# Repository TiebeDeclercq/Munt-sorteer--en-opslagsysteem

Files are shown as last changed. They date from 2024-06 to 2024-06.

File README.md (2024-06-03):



<!-- PROJECT LOGO -->
<br />
<div align="center">
  <a href="https://github.com/othneildrew/Best-README-Template">
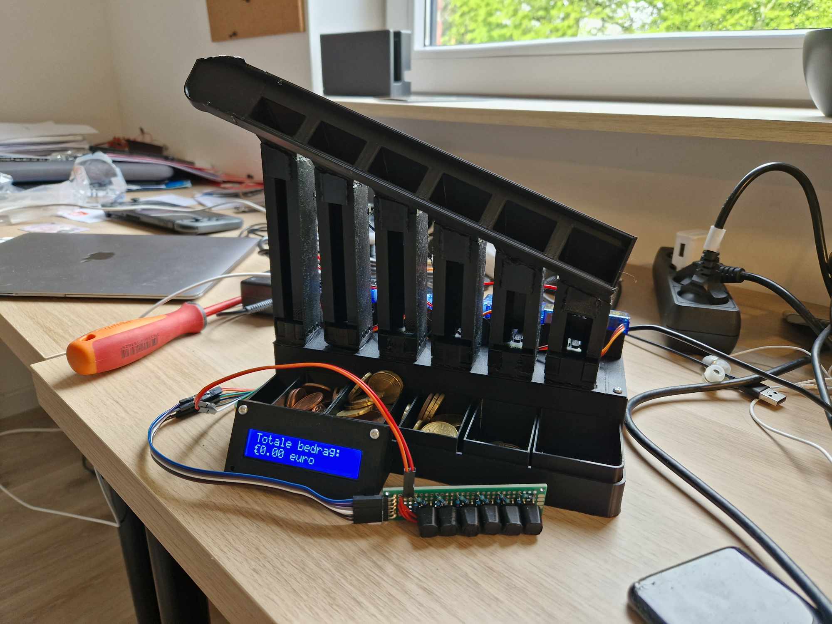
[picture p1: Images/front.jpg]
front sorter
    
  </a>

  <h3 align="center">Coin sorting and storage system</h3>

  <p align="center">
    A coin-counting, storing, and dispensing system.
    <br />
    <a href="https://giptiebedeclercq.wordpress.com/"><strong>View the blog »</strong></a>
    <br />
    <br />
  </p>
</div>

<!-- ABOUT THE PROJECT -->
## About The Project

My design is a coin sorting and storage system aimed at effectively addressing the issue of loose change in the household. By storing all your coins in one central location, all the inconveniences of scattered small change are eliminated, and you have an accurate overview of your available loose change at all times. In this document, I will meticulously walk through the various phases of the project, detailing the development and implementation of the coin sorting and storage system step by step. All necessary information, including components and diagrams, is included in my document, accompanied by comprehensive explanations for a clear overview of the entire process.

## Download the software
This is the general software to control the coinsorting system for simply storing you're coins
<p float="left">
  
  
  
</p>

This is sofware/game to play flappy bird but you can play with multiple people and compete against eatchother 



<p align="right">(<a href="#readme-top">back to top</a>)</p>

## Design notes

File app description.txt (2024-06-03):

Deze app is een toevoeging op het muntsorteer- en opslagsysteem gemaakt door Ti3b3:

Krijg een overzicht van al je kleingeld
Kies hoeveel kleingeld je wilt uitwerpen
Personaliseer je muntsorteerder tot je behoefte!

MAXIMAAL AANTAL KLEINGELD INSTELLEN
Wil je maar een maximaal aantal geld toelaten in het systeem? Geen probleem dit kan je allemaal instellen via deze app

EEN EXACTE HOEVEELHEID KLEINGELD UITWERPEN
Via deze app kan je een hoeveelheid ingeven en er zal berekent worden of dit mogelijk is en zal dan uitgeworpen worden!

ZIT ER EEN PROBLEEM IN JE OPSTELLING?
Je kan de waarden van je geldsysteem aanpassen als ze verkeerd gedecteerd zijn en ook je maximale waarden aanpassen!

EEN ANDERE WERKINGSMODUS INSTELLEN?
Je kan je werkingsmodus instellen via de app als je bevoorbeeld wilt dat hij enkel sorteert en niet opslaat of geluid maakt bij het uitwerpen.

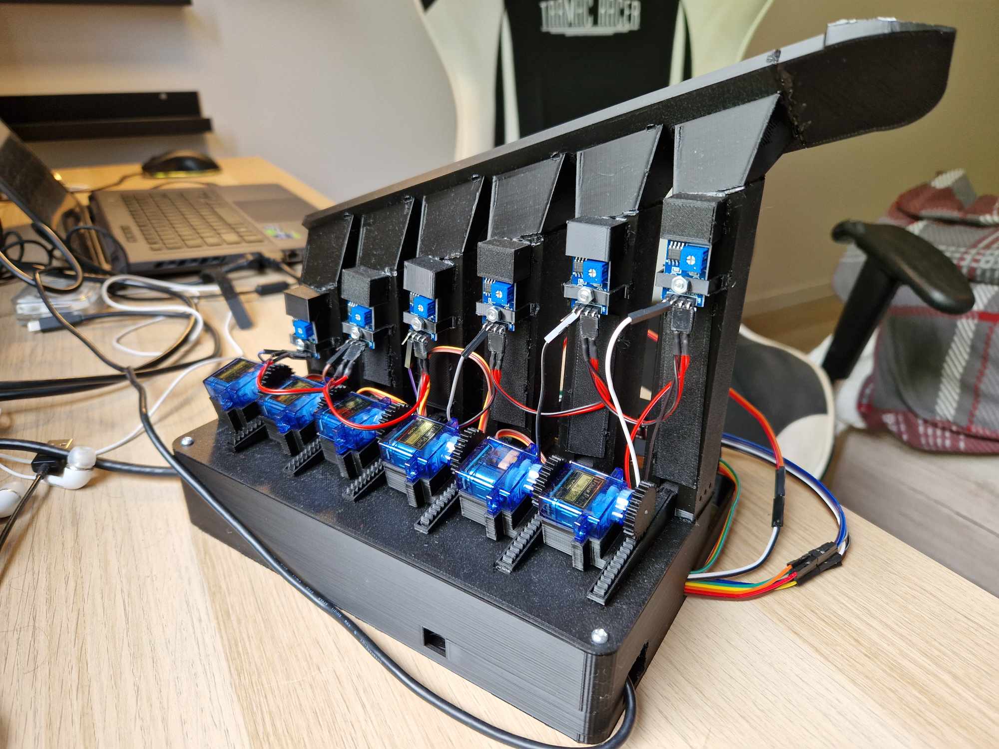
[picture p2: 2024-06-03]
Images/back.jpg

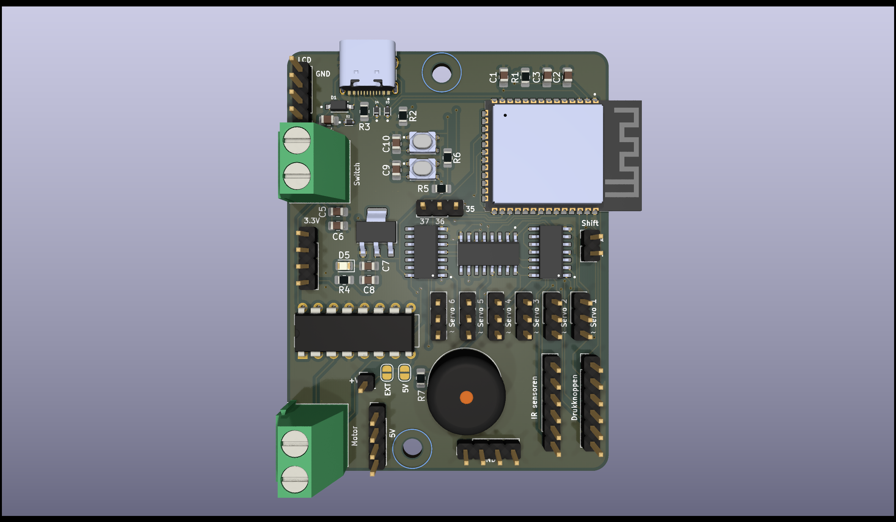
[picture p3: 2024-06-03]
Images/MuntsorteerderESPbord.png

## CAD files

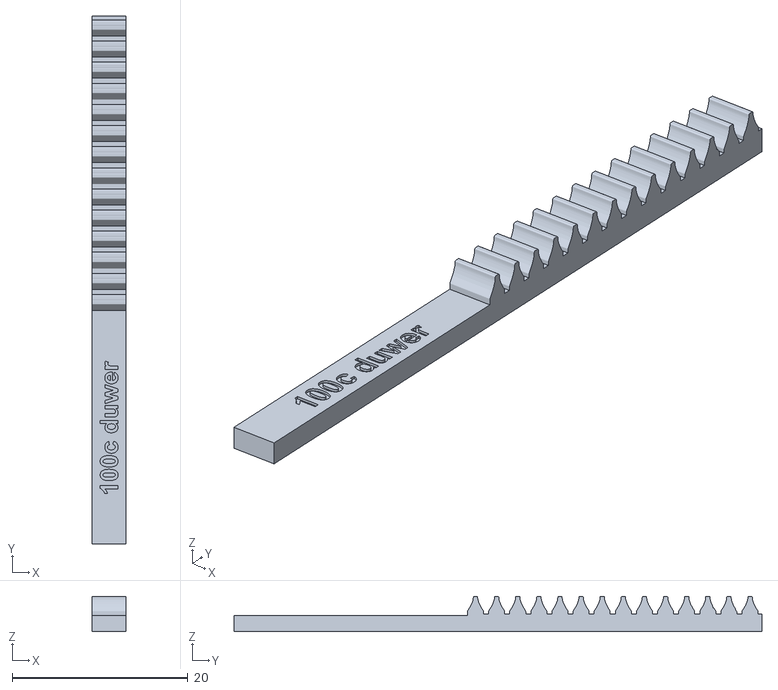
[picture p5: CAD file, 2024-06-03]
Printables/1eurSlider.stl
3.85 x 60.0 x 4.02

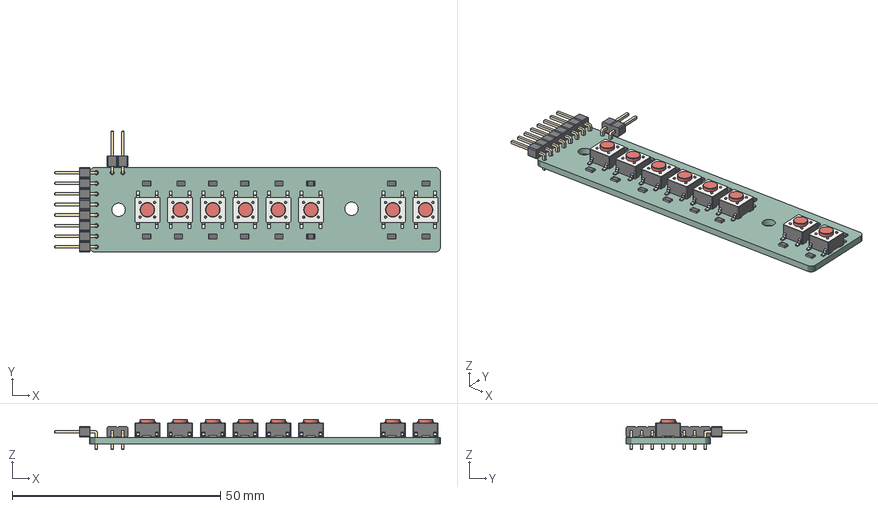
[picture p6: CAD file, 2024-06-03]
SeperatePCB's/ButtonsPCB/ButtonsPCB.step
92.6 x 29.1 x 7.30 mm
_autosave-ButtonsPCB PCB

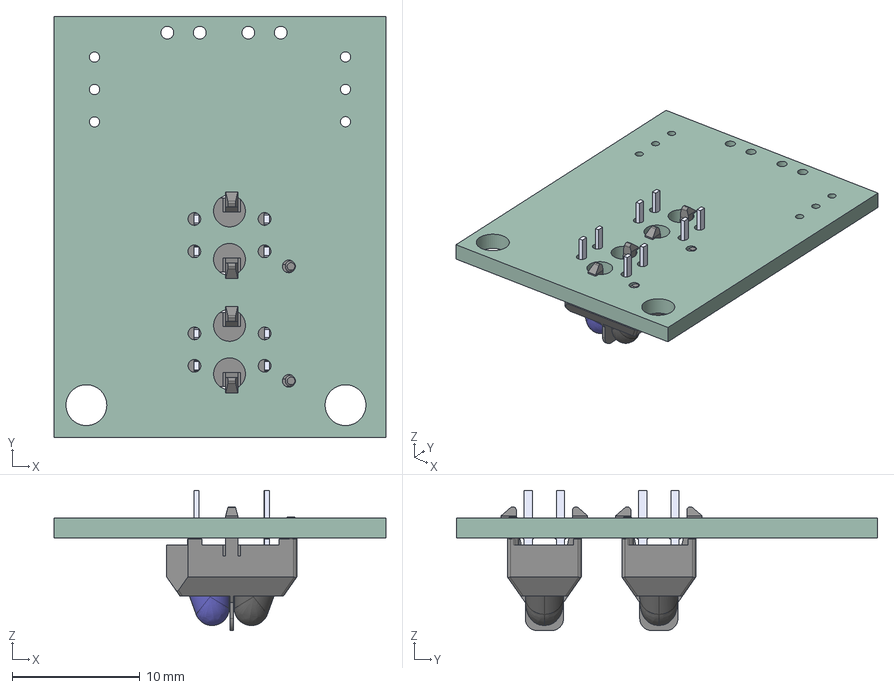
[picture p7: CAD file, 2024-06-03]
SeperatePCB's/IrBoards/IrBoards.step
26.0 x 33.0 x 11.0 mm
_autosave-IrBoards PCB

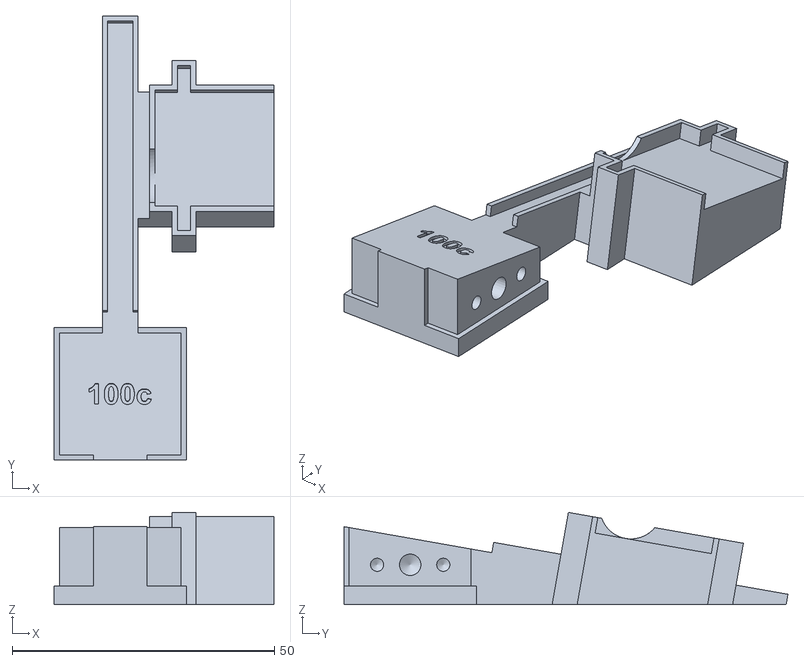
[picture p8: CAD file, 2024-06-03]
Printables/1eurPushout.stl
41.9 x 84.7 x 17.6

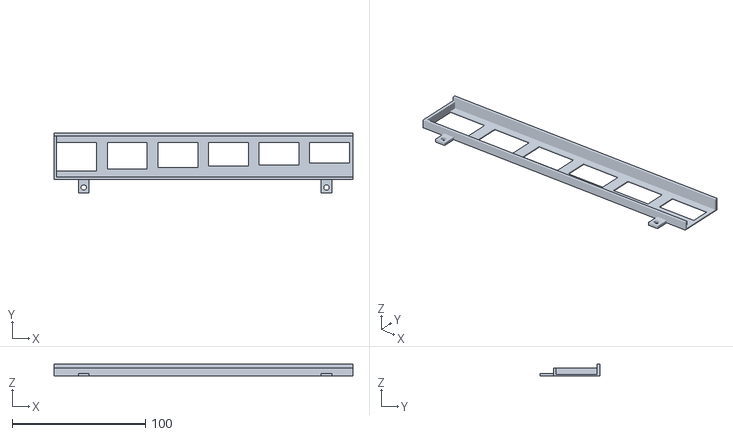
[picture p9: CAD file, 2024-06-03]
Printables/Sorter.stl
224.5 x 44.8 x 9.00

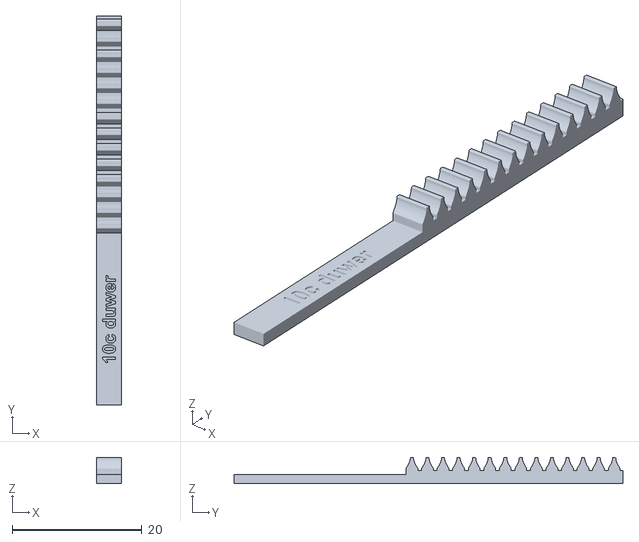
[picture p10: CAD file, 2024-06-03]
Printables/10centSlider.stl
3.85 x 60.0 x 4.02

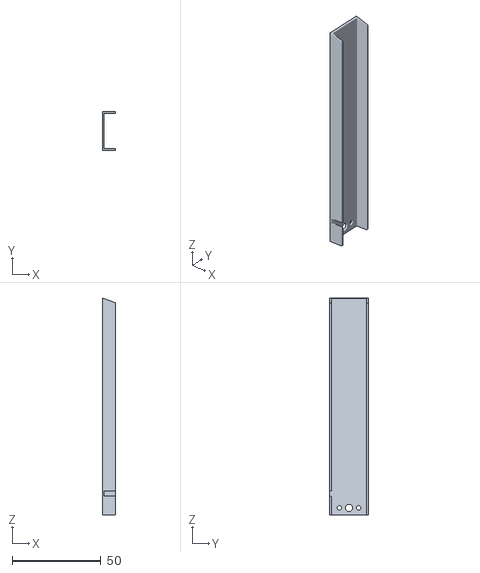
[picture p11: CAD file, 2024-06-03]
Printables/10centRightWall.stl
7.50 x 21.8 x 122.2

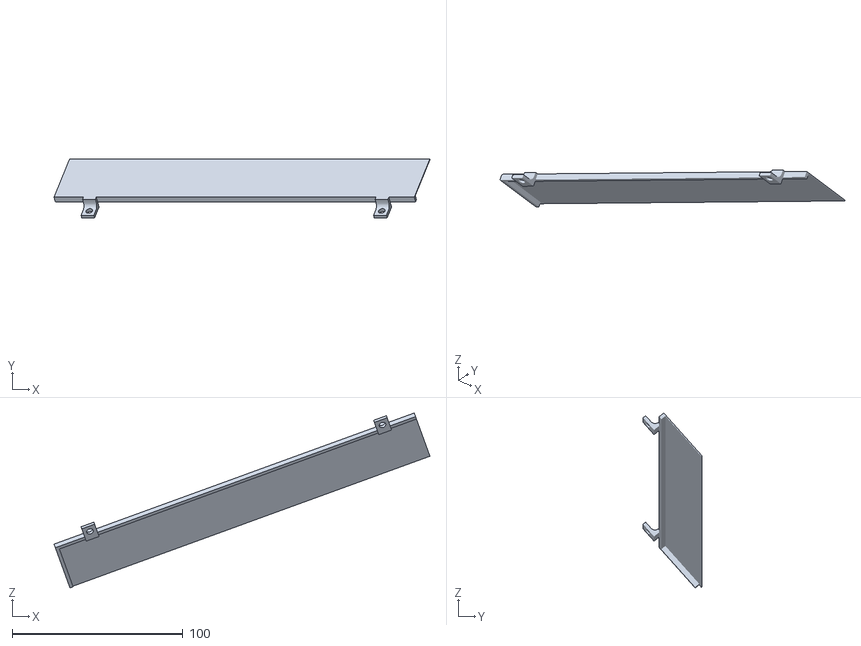
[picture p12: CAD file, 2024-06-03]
Printables/SorterCover.stl
220.2 x 34.5 x 102.5

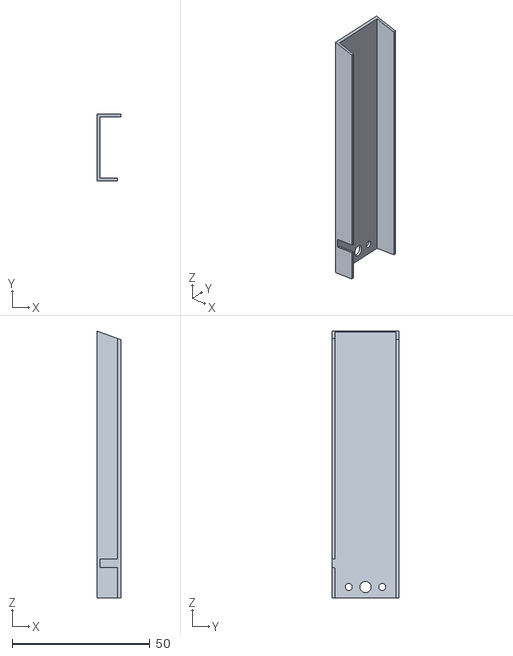
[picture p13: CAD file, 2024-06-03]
Printables/20centRightWall.stl
8.70 x 24.2 x 96.7

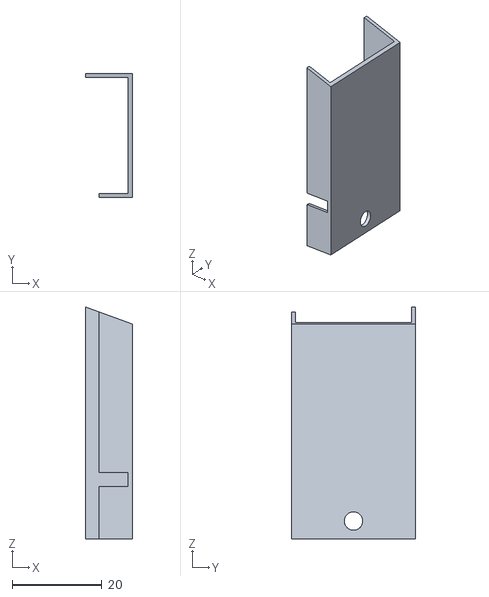
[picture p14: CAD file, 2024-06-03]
Printables/2eurLeftWall.stl
10.4 x 27.8 x 51.7

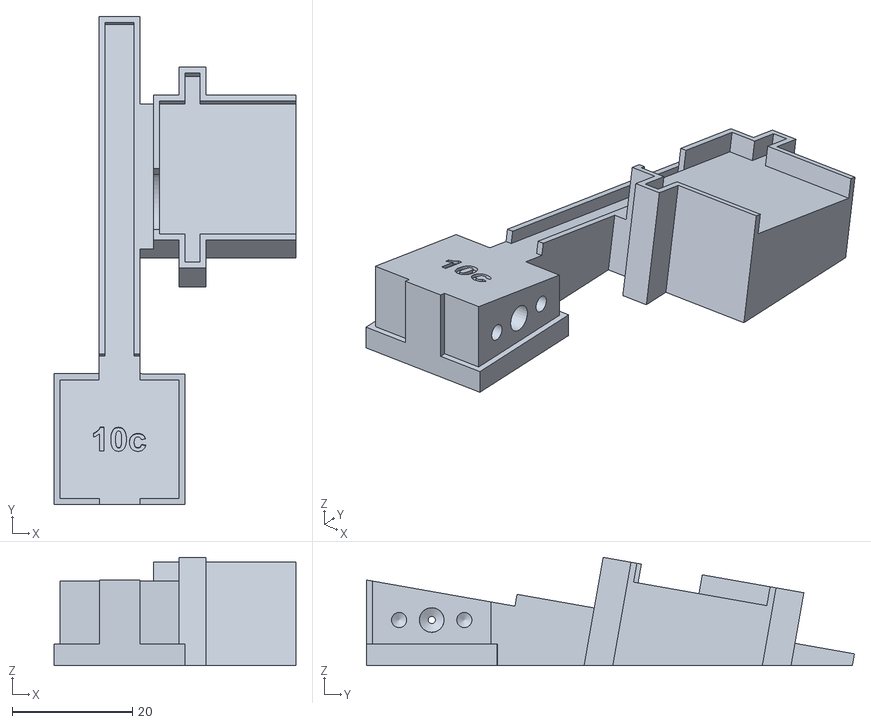
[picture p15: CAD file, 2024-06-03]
Printables/10cPushout.stl
40.2 x 81.2 x 18.0

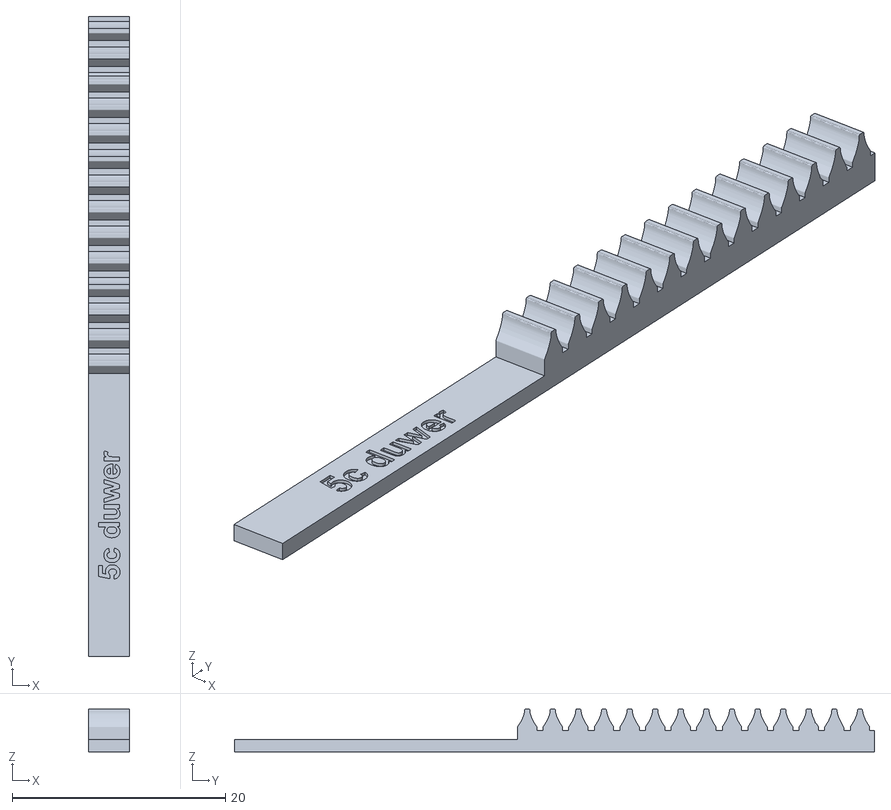
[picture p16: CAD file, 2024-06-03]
Printables/5centSlider.stl
3.85 x 60.0 x 4.02

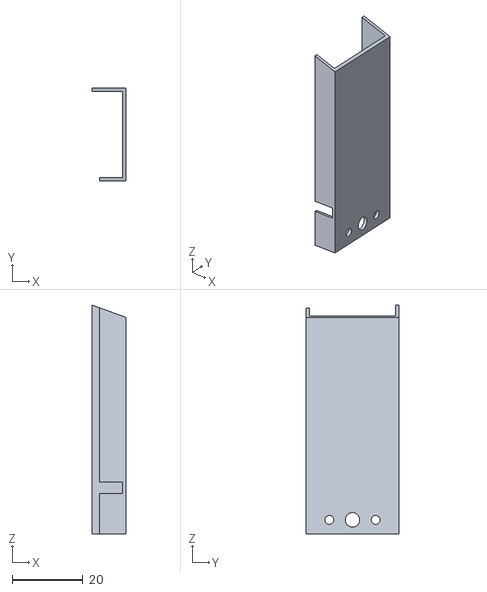
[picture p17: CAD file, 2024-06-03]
Printables/50centLeftWall.stl
9.70 x 26.2 x 64.9

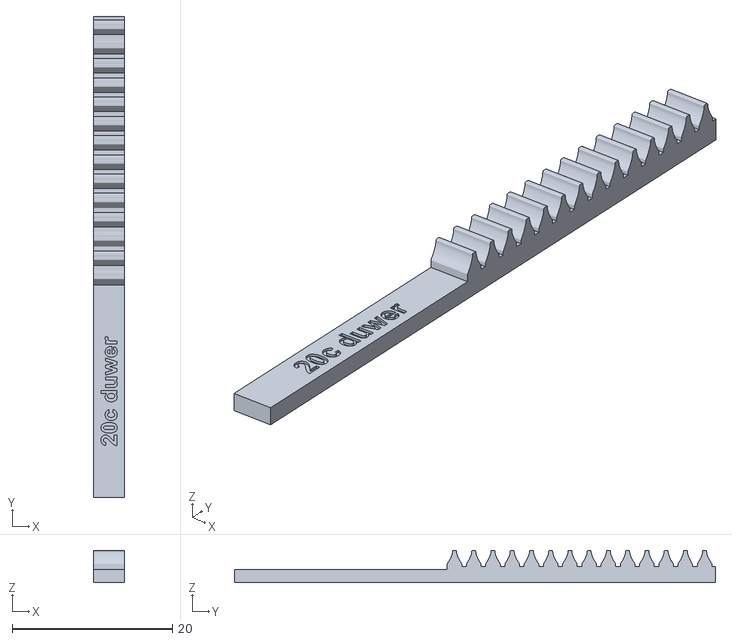
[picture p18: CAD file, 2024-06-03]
Printables/20centSlider.stl
3.85 x 60.0 x 4.02

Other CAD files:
Printables/50centRightWall.stl
Printables/2eurSlider.stl
Printables/5centRightWall.stl
Printables/2eurPushout.stl
Printables/10centLeftWall.stl
Printables/10centTunnel.stl
Printables/1eurLeftWall.stl
Printables/1eurRightWall.stl
Printables/1eurTunnel.stl
Printables/20centLeftWall.stl
Printables/20centPushout.stl
Printables/20centTunnel.stl
Printables/2eurRightWall.stl
Printables/2eurTunnel.stl
Printables/50centPushout.stl
Printables/50centSlider.stl
Printables/50centTunnel.stl
Printables/5centLeftWall.stl
Printables/5centPushout.stl
Printables/5centTunnel.stl
Printables/BoxWithButtons.stl
Printables/Cover.stl
Printables/IrHead.stl
Printables/IrHolder.stl
Printables/LCDcover.stl
Printables/Lid.stl
Printables/ServoGear.stl

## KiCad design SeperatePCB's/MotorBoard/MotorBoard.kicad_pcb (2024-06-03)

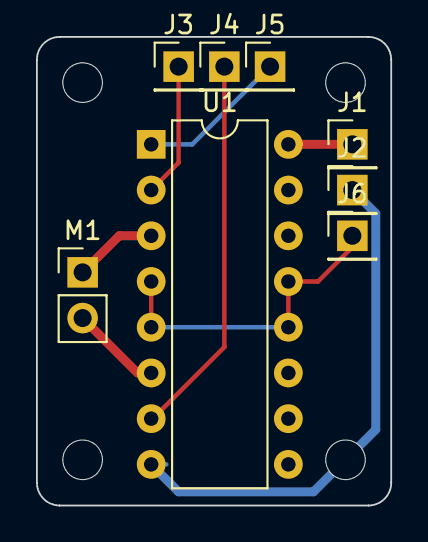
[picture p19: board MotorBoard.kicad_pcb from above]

Board: 2 copper layers, 19.7 x 26.0 mm, 12 parts (0 on the bottom side), 8 nets.

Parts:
H1, H2, H3, H4: MountingHole; MountingHole_2.2mm_M2
J1, J2, J3, J4, J5, J6: Conn_01x01_Pin; PinHeader_1x01_P2.54mm_Vertical
M1: Motor_DC; PinHeader_1x02_P2.54mm_Vertical
U1: L293D; DIP-16_W7.62mm

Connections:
unnamed: J1.1, U1.16 (VCC1)
unnamed: J2.1, U1.8 (VCC2)
unnamed: J3.1, U1.2 (1A)
unnamed: J4.1, U1.7 (2A)
unnamed: J5.1, U1.1 (EN1,2)
unnamed: J6.1, U1.4 (GND), U1.5 (GND), U1.12 (GND), U1.13 (GND)
unnamed: M1.1 (+), U1.3 (1Y)
unnamed: M1.2 (-), U1.6 (2Y)

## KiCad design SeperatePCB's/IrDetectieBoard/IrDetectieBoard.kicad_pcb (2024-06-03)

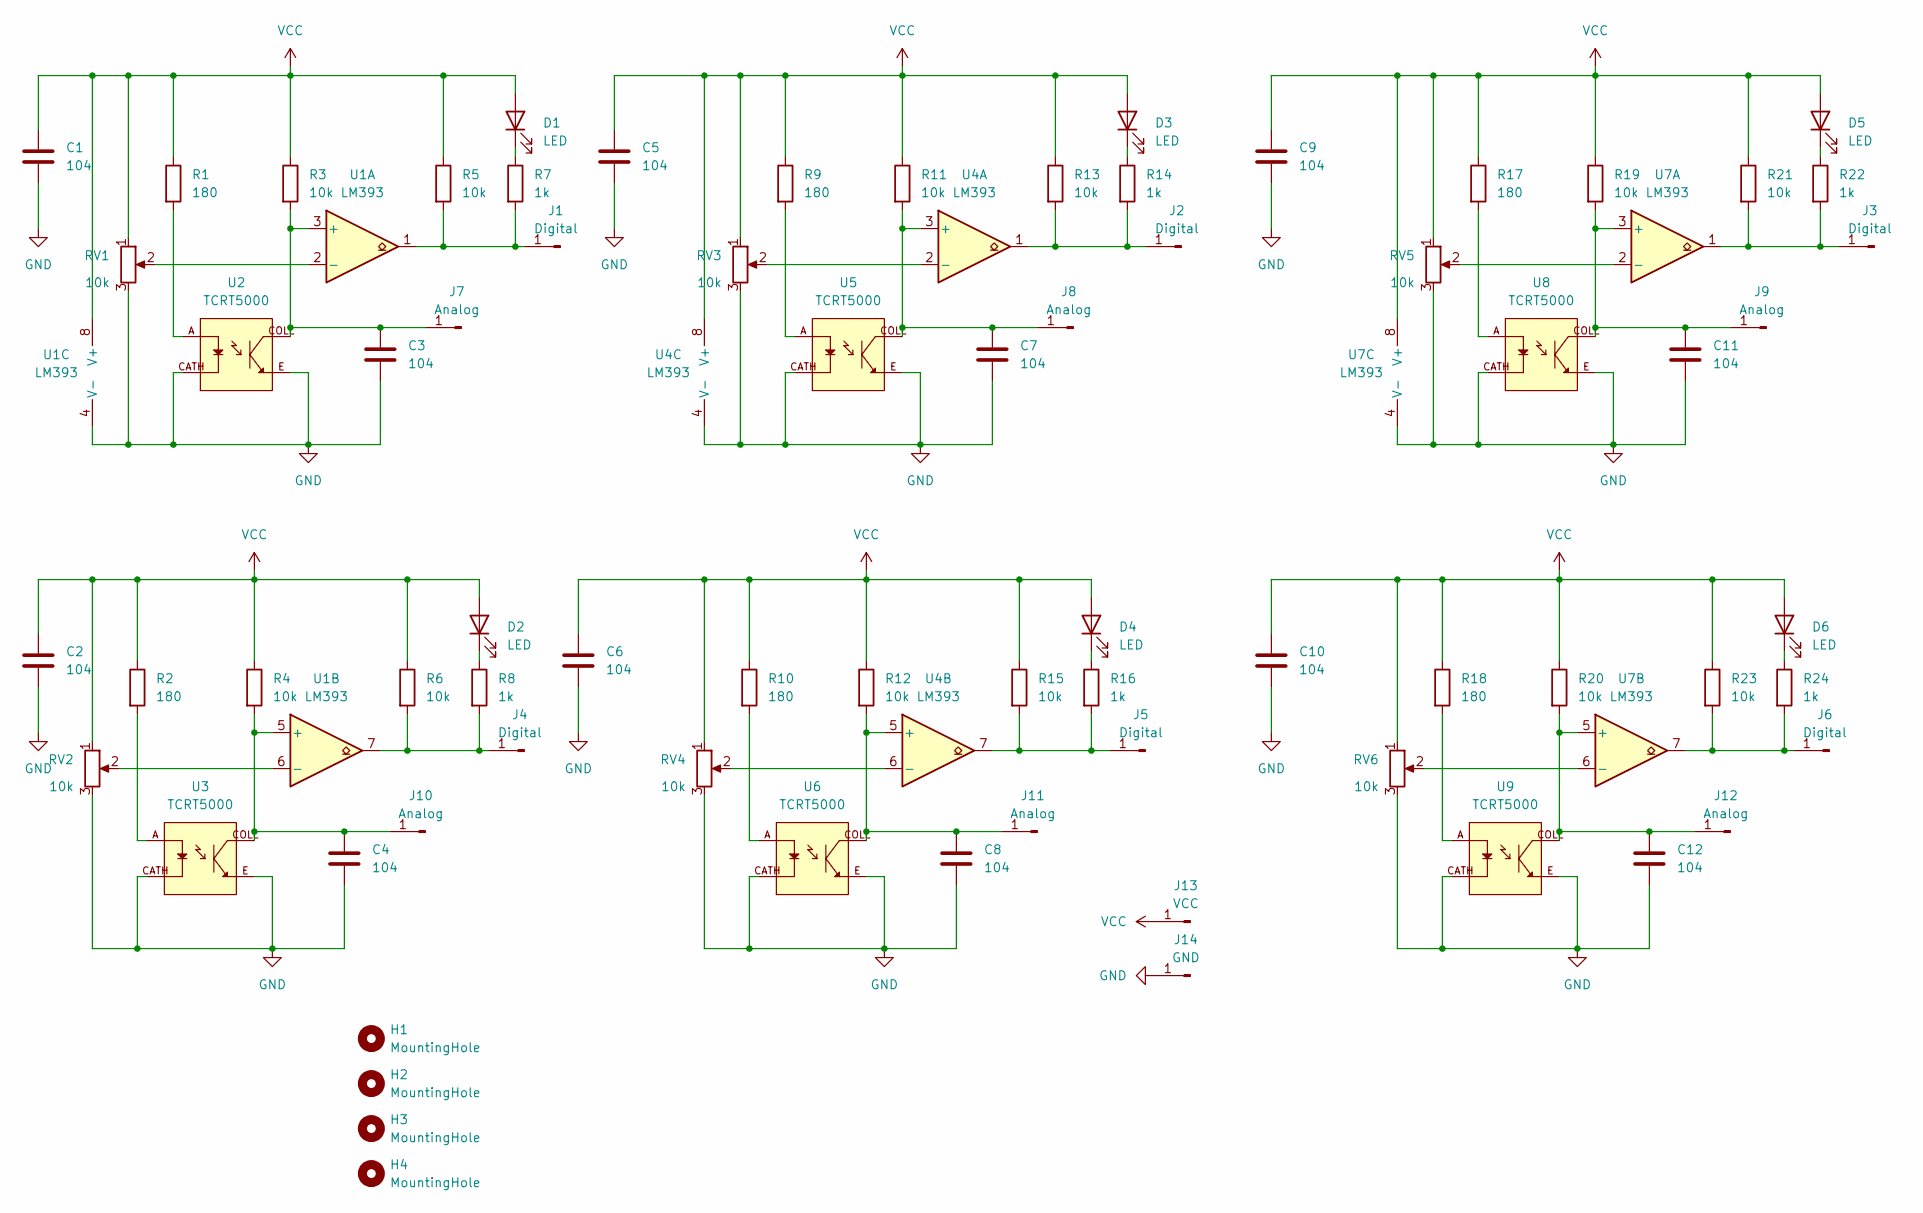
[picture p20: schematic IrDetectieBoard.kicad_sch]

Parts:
C1, C2, C3, C4, C5, C6, C7, C8, C9, C10, C11, C12: 104; C_0805_2012Metric_Pad1.18x1.45mm_HandSolder
D1, D2, D3, D4, D5, D6: LED; LED_0805_2012Metric_Pad1.15x1.40mm_HandSolder
H1, H2, H3, H4: MountingHole; MountingHole_2.2mm_M2
J1, J2, J3, J4, J5, J6: Digital; PinHeader_1x01_P2.54mm_Vertical
J7, J8, J9, J10, J11, J12: Analog; PinHeader_1x01_P2.54mm_Vertical
J13: VCC; PinHeader_1x01_P2.54mm_Vertical
J14: GND; PinHeader_1x01_P2.54mm_Vertical
R1, R2, R9, R10, R17, R18: 180; R_0805_2012Metric_Pad1.20x1.40mm_HandSolder
R3, R4, R5, R6, R11, R12, R13, R15, R19, R20, R21, R23: 10k; R_0805_2012Metric_Pad1.20x1.40mm_HandSolder
R7, R8, R14, R16, R22, R24: 1k; R_0805_2012Metric_Pad1.20x1.40mm_HandSolder
RV1, RV2, RV3, RV4, RV5, RV6: 10k; Potentiometer_Bourns_3296W_Vertical
U1, U4, U7: LM393; SO-8_3.9x4.9mm_P1.27mm
U2, U3, U5, U6, U8, U9: TCRT5000; PARTREV 1.7

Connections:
GND: C1.2, C2.2, C3.2, C4.2, C5.2, C6.2, C7.2, C8.2, C9.2, C10.2, C11.2, C12.2, J14.1, RV1.3, RV2.3, RV3.3, RV4.3, RV5.3, RV6.3, U1.4 (V-), U2.CATH, U2.E, U3.CATH, U3.E, U4.4 (V-), U5.CATH, U5.E, U6.CATH, U6.E, U7.4 (V-), U8.CATH, U8.E, U9.CATH, U9.E
unnamed: D1.1 (K), R7.1
unnamed: D2.1 (K), R8.1
unnamed: D3.1 (K), R14.1
unnamed: D4.1 (K), R16.1
unnamed: D5.1 (K), R22.1
unnamed: D6.1 (K), R24.1
unnamed: J1.1, R5.2, R7.2, U1.1
unnamed: J2.1, R13.2, R14.2, U4.1
unnamed: J3.1, R21.2, R22.2, U7.1
unnamed: J4.1, R6.2, R8.2, U1.7
unnamed: J5.1, R15.2, R16.2, U4.7
unnamed: J6.1, R23.2, R24.2, U7.7
unnamed: C3.1, J7.1, R3.2, U1.3 (+), U2.COLL
unnamed: C7.1, J8.1, R11.2, U4.3 (+), U5.COLL
unnamed: C11.1, J9.1, R19.2, U7.3 (+), U8.COLL
unnamed: C4.1, J10.1, R4.2, U1.5 (+), U3.COLL
unnamed: C8.1, J11.1, R12.2, U4.5 (+), U6.COLL
unnamed: C12.1, J12.1, R20.2, U7.5 (+), U9.COLL
unnamed: R1.2, U2.A
unnamed: R2.2, U3.A
unnamed: R9.2, U5.A
unnamed: R10.2, U6.A
unnamed: R17.2, U8.A
unnamed: R18.2, U9.A
unnamed: RV1.2, U1.2 (-)
unnamed: RV2.2, U1.6 (-)
unnamed: RV3.2, U4.2 (-)
unnamed: RV4.2, U4.6 (-)
unnamed: RV5.2, U7.2 (-)
unnamed: RV6.2, U7.6 (-)
VCC: C1.1, C2.1, C5.1, C6.1, C9.1, C10.1, D1.2 (A), D2.2 (A), D3.2 (A), D4.2 (A), D5.2 (A), D6.2 (A), J13.1, R1.1, R2.1, R3.1, R4.1, R5.1, R6.1, R9.1, R10.1, R11.1, R12.1, R13.1, R15.1, R17.1, R18.1, R19.1, R20.1, R21.1, R23.1, RV1.1, RV2.1, RV3.1, RV4.1, RV5.1, RV6.1, U1.8 (V+), U4.8 (V+), U7.8 (V+)

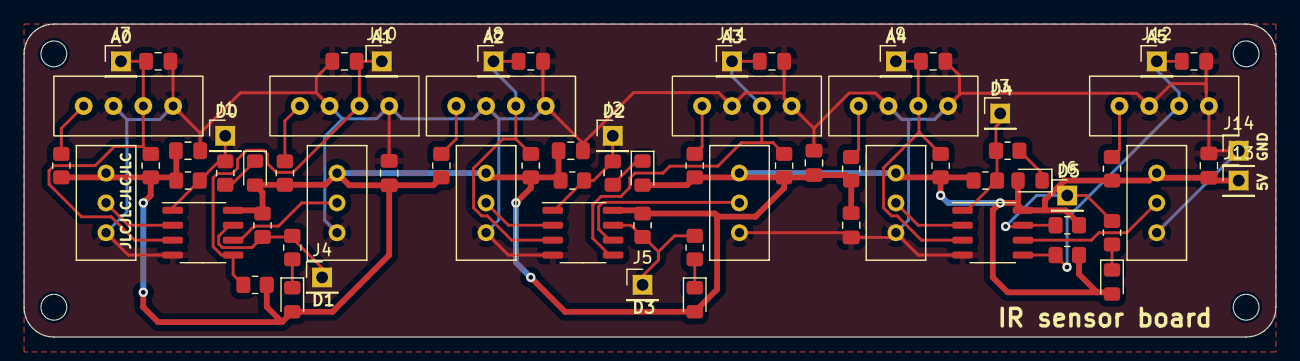
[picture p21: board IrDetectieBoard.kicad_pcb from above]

Board: 2 copper layers, 106.7 x 26.7 mm, 75 parts (0 on the bottom side), 32 nets.

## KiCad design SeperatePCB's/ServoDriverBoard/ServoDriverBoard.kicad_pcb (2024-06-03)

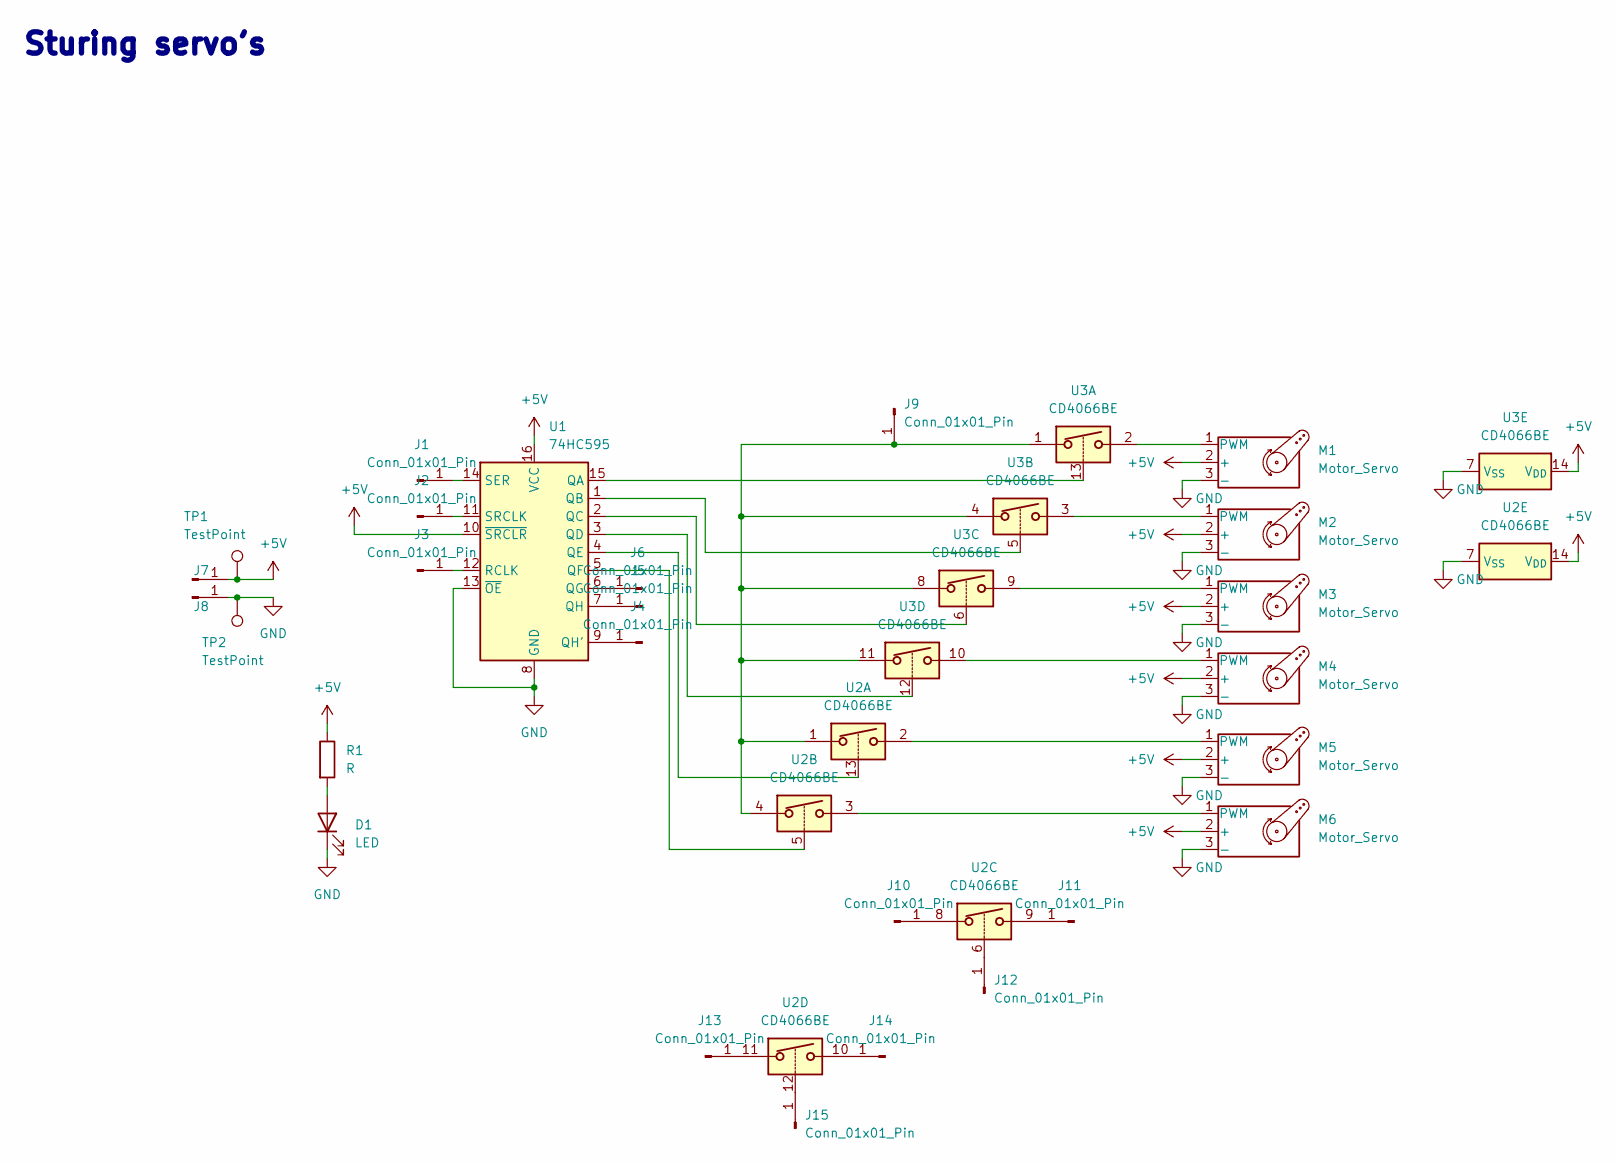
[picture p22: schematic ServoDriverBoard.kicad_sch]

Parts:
D1: LED; LED_0805_2012Metric_Pad1.15x1.40mm_HandSolder
J1, J2, J3, J4, J5, J6, J7, J8, J9, J10, J11, J12, J13, J14, J15: Conn_01x01_Pin; PinHeader_1x01_P2.54mm_Vertical
M1, M2, M3, M4, M5, M6: Motor_Servo; PinHeader_1x03_P2.54mm_Vertical
R1: R; R_0805_2012Metric_Pad1.20x1.40mm_HandSolder
TP1, TP2: TestPoint; TestPoint_Pad_D1.5mm
U1: 74HC595; DIP-16_W7.62mm_Socket
U2, U3: CD4066BE; DIP-14_W7.62mm_Socket

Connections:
+5V: J7.1, M1.2 (+), M2.2 (+), M3.2 (+), M4.2 (+), M5.2 (+), M6.2 (+), R1.1, TP1.1, U1.10 (~SRCLR), U1.16 (VCC), U2.14 (V_{DD}), U3.14 (V_{DD})
GND: D1.1 (K), J8.1, M1.3 (-), M2.3 (-), M3.3 (-), M4.3 (-), M5.3 (-), M6.3 (-), TP2.1, U1.8 (GND), U1.13 (~OE), U2.7 (V_{SS}), U3.7 (V_{SS})
unnamed: D1.2 (A), R1.2
unnamed: J1.1, U1.14 (SER)
unnamed: J2.1, U1.11 (SRCLK)
unnamed: J3.1, U1.12 (RCLK)
unnamed: J4.1, U1.9 (QH')
unnamed: J5.1, U1.7 (QH)
unnamed: J6.1, U1.6 (QG)
unnamed: J9.1, U2.1, U2.4, U3.1, U3.4, U3.8, U3.11
unnamed: J10.1, U2.8
unnamed: J11.1, U2.9
unnamed: J12.1, U2.6
unnamed: J13.1, U2.11
unnamed: J14.1, U2.10
unnamed: J15.1, U2.12
unnamed: M1.1 (PWM), U3.2
unnamed: M2.1 (PWM), U3.3
unnamed: M3.1 (PWM), U3.9
unnamed: M4.1 (PWM), U3.10
unnamed: M5.1 (PWM), U2.2
unnamed: M6.1 (PWM), U2.3
unnamed: U1.15 (QA), U3.13
unnamed: U1.1 (QB), U3.5
unnamed: U1.2 (QC), U3.6
unnamed: U1.3 (QD), U3.12
unnamed: U1.4 (QE), U2.13
unnamed: U1.5 (QF), U2.5

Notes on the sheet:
Sturing servo's

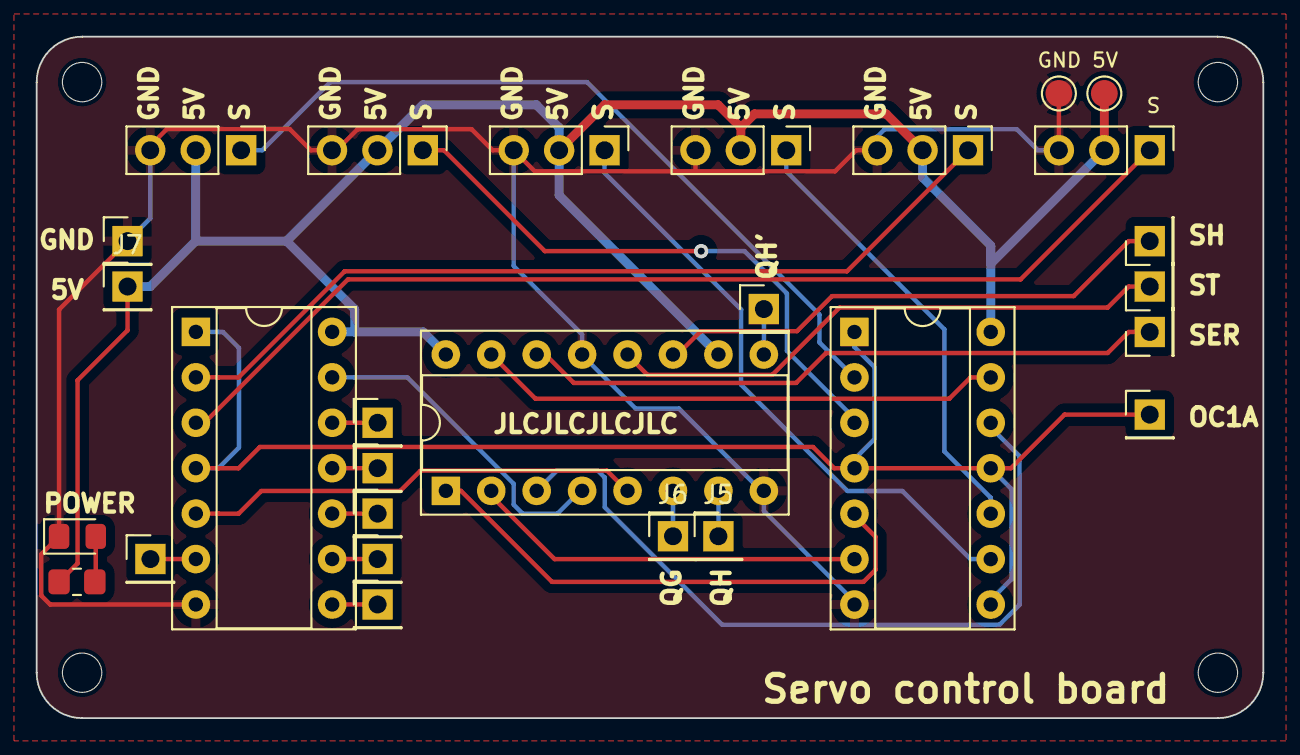
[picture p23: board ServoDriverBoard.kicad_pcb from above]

Board: 2 copper layers, 68.6 x 38.1 mm, 32 parts (0 on the bottom side), 28 nets.

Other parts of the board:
H1, H2, H3, H4: MountingHole; MountingHole_2.2mm_M2

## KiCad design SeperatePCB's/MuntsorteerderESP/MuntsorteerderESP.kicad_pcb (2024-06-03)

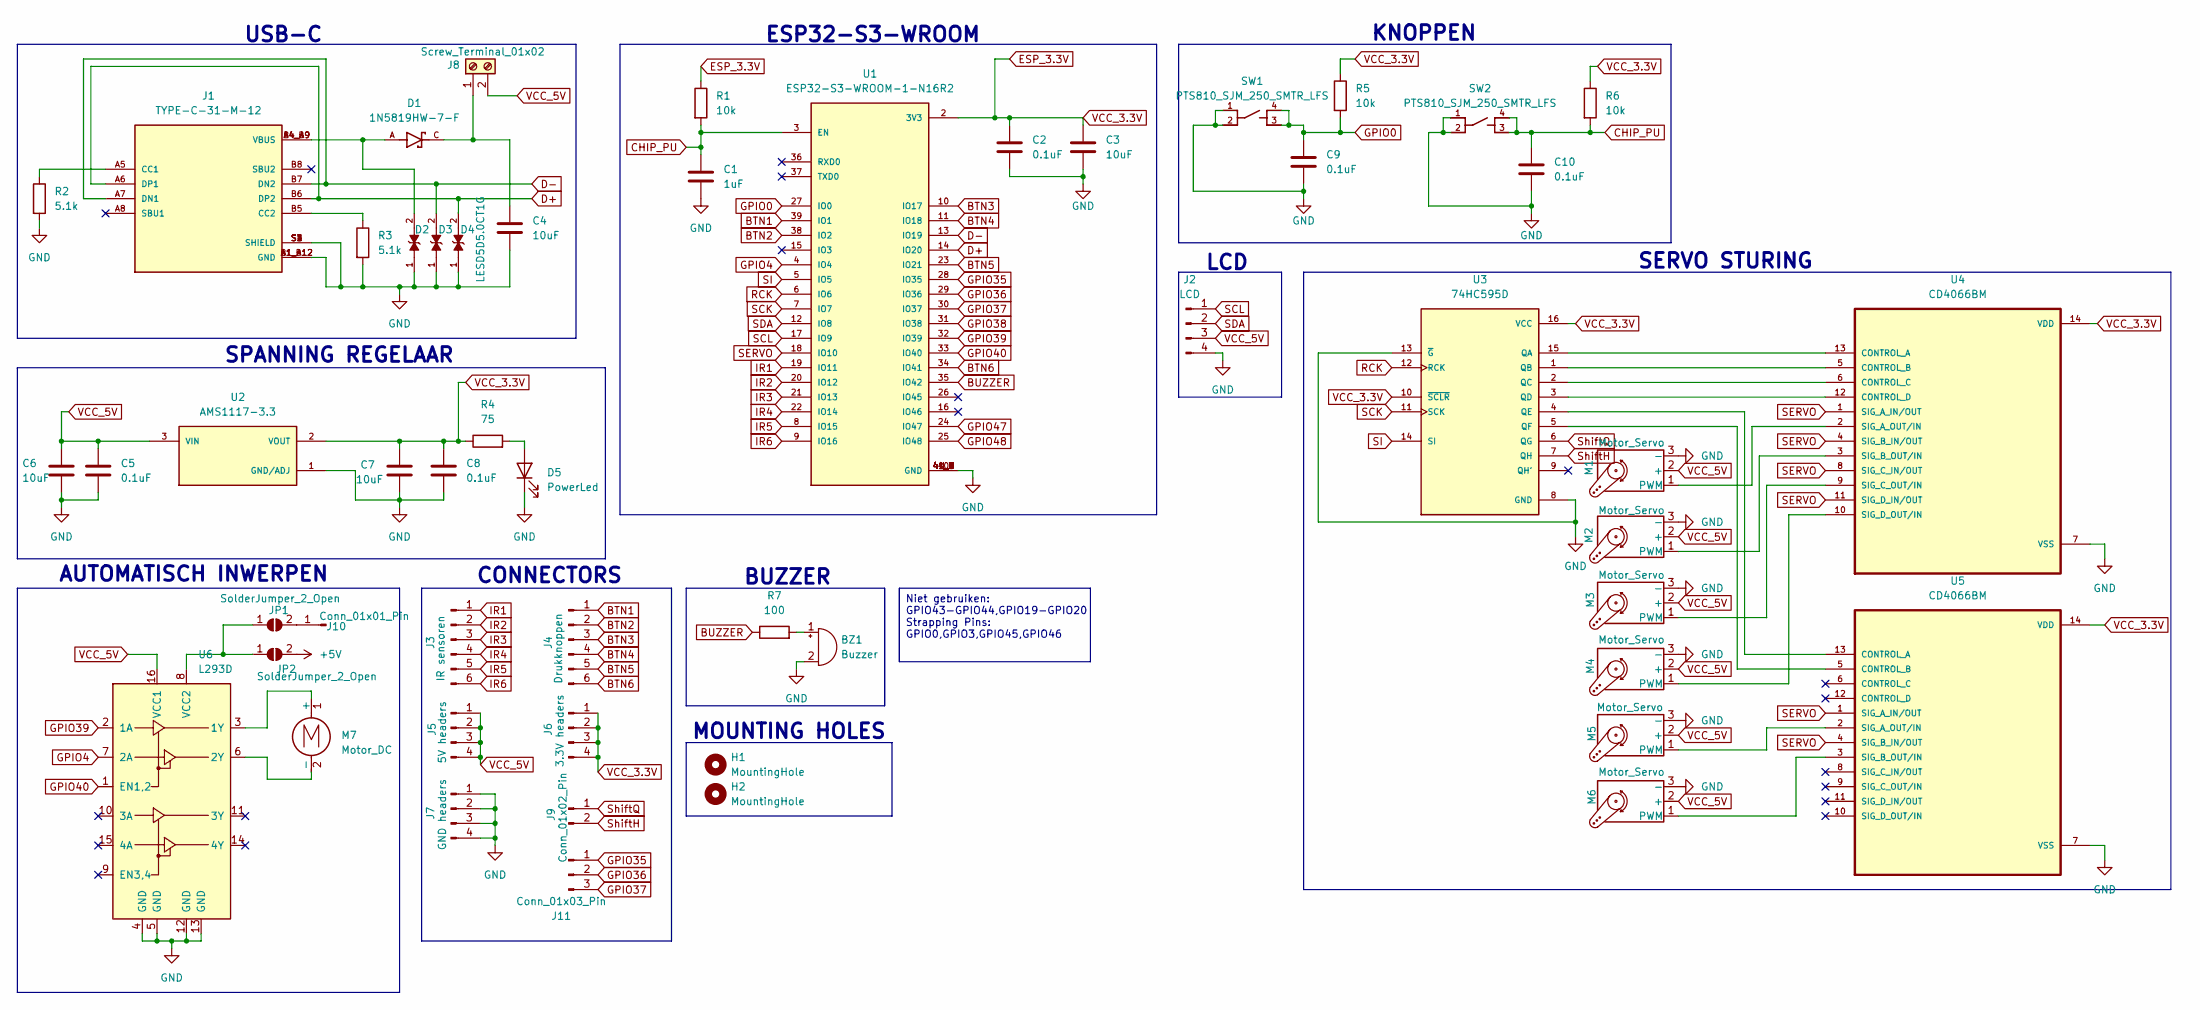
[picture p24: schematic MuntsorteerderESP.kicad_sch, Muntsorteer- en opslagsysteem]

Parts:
BZ1: Buzzer; Buzzer_12x9.5RM7.6
C1: 1uF; C_0805_2012Metric_Pad1.18x1.45mm_HandSolder
C2, C5, C8, C9, C10: 0.1uF; C_0805_2012Metric_Pad1.18x1.45mm_HandSolder
C3, C4, C6, C7: 10uF; C_0805_2012Metric_Pad1.18x1.45mm_HandSolder
D1: 1N5819HW-7-F; SOD3715X145N; PARTREV 18-2
D2, D3, D4: LESD5D5.0CT1G; TVS_LESD5D5.0CT1G; PARTREV O
D5: PowerLed; LED_0805_2012Metric
H1, H2: MountingHole; MountingHole_3.2mm_M3
J1: TYPE-C-31-M-12; HRO_TYPE-C-31-M-12; PARTREV 2020.12.08
J2: LCD; PinHeader_1x04_P2.54mm_Vertical
J3: IR sensoren; PinHeader_1x06_P2.54mm_Vertical
J4: Drukknoppen; PinHeader_1x06_P2.54mm_Vertical
J5: 5V headers; PinHeader_1x04_P2.54mm_Vertical
J6: 3.3V headers; PinHeader_1x04_P2.54mm_Vertical
J7: GND headers; PinHeader_1x04_P2.54mm_Vertical
J8: Screw_Terminal_01x02; TerminalBlock_Phoenix_MKDS-1,5-2-5.08_1x02_P5.08mm_Horizont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
J9: Conn_01x02_Pin; PinHeader_1x02_P2.54mm_Vertical
J10: Conn_01x01_Pin; PinHeader_1x01_P2.54mm_Vertical
J11: Conn_01x03_Pin; PinHeader_1x03_P2.54mm_Vertical
JP1, JP2: SolderJumper_2_Open; SolderJumper-2_P1.3mm_Open_RoundedPad1.0x1.5mm
M1, M2, M3, M4, M5, M6: Motor_Servo; PinHeader_1x03_P2.54mm_Vertical
M7: Motor_DC; TerminalBlock_Phoenix_MKDS-1,5-2-5.08_1x02_P5.08mm_Horizont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
R1, R5, R6: 10k; R_0805_2012Metric_Pad1.20x1.40mm_HandSolder
R2, R3: 5.1k; R_0805_2012Metric_Pad1.20x1.40mm_HandSolder
R4: 75; R_0805_2012Metric_Pad1.20x1.40mm_HandSolder
R7: 100; R_0805_2012Metric_Pad1.20x1.40mm_HandSolder
SW1, SW2: PTS810_SJM_250_SMTR_LFS; SW_PTS810_SJM_250_SMTR_LFS
U1: ESP32-S3-WROOM-1-N16R2; XCVR_ESP32-S3-WROOM-1-N16R2; PARTREV v1.0
U2: AMS1117-3.3; SOT229P700X180-4N; PARTREV N/A
U3: 74HC595D; SOP127P600X175-16N; PARTREV 4.0
U4, U5: CD4066BM; SOIC127P600X175-14N
U6: L293D; DIP-16_W7.62mm

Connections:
+5V: JP2.2 (B)
BTN1: J4.1, U1.39 (IO1)
BTN2: J4.2, U1.38 (IO2)
BTN3: J4.3, U1.10 (IO17)
BTN4: J4.4, U1.11 (IO18)
BTN5: J4.5, U1.23 (IO21)
BTN6: J4.6, U1.34 (IO41)
BUZZER: R7.1, U1.35 (IO42)
CHIP_PU: C1.1, C10.1, R1.2, R6.2, SW2.3, SW2.4, U1.3 (EN)
D+: D4.2, J1.A6 (DP1), J1.B6 (DP2), U1.14 (IO20)
D-: D3.2, J1.A7 (DN1), J1.B7 (DN2), U1.13 (IO19)
ESP_3.3V: C2.1, C3.1, C7.1, C8.1, J6.1, J6.2, J6.3, J6.4, R1.1, R4.1, R5.1, R6.1, U1.2 (3V3), U2.2 (VOUT), U3.10 (~SCLR), U3.16 (VCC), U4.14 (VDD), U5.14 (VDD)
GND: BZ1.2 (+), C1.2, C2.2, C3.2, C4.2, C5.2, C6.2, C7.2, C8.2, C9.2, C10.2, D2.1, D3.1, D4.1, D5.1 (K), J1.A1_B12 (GND), J1.B1_A12 (GND), J1.S1 (SHIELD), J1.S2 (SHIELD), J1.S3 (SHIELD), J1.S4 (SHIELD), J2.4, J7.1, J7.2, J7.3, J7.4, M1.3 (-), M2.3 (-), M3.3 (-), M4.3 (-), M5.3 (-), M6.3 (-), R2.2, R3.2, SW1.1, SW1.2, SW2.1, SW2.2, U1.1 (GND), U1.40 (GND), U1.41_1 (GND), U1.41_2 (GND), U1.41_3 (GND), U1.41_4 (GND), U1.41_5 (GND), U1.41_6 (GND), U1.41_7 (GND), U1.41_8 (GND), U1.41_9 (GND), U2.1 (GND/ADJ), U3.8 (GND), U3.13 (~G), U4.7 (VSS), U5.7 (VSS), U6.4 (GND), U6.5 (GND), U6.12 (GND), U6.13 (GND)
GPIO0: C9.1, R5.2, SW1.3, SW1.4, U1.27 (IO0)
GPIO4: U1.4 (IO4), U6.7 (2A)
GPIO35: J11.1, U1.28 (IO35)
GPIO36: J11.2, U1.29 (IO36)
GPIO37: J11.3, U1.30 (IO37)
GPIO38: U1.31 (IO38)
GPIO39: U1.32 (IO39), U6.2 (1A)
GPIO40: U1.33 (IO40), U6.1 (EN1,2)
GPIO47: U1.24 (IO47)
GPIO48: U1.25 (IO48)
IR1: J3.1, U1.19 (IO11)
IR2: J3.2, U1.20 (IO12)
IR3: J3.3, U1.21 (IO13)
IR4: J3.4, U1.22 (IO14)
IR5: J3.5, U1.8 (IO15)
IR6: J3.6, U1.9 (IO16)
unnamed: BZ1.1 (-), R7.2
unnamed: D1.A, D2.2, J1.A4_B9 (VBUS), J1.B4_A9 (VBUS)
unnamed: D5.2 (A), R4.2
unnamed: J1.A5 (CC1), R2.1
unnamed: J1.B5 (CC2), R3.1
unnamed: C4.1, D1.C, J8.1
unnamed: J10.1, JP1.2 (B)
unnamed: JP1.1 (A), JP2.1 (A), U6.8 (VCC2)
unnamed: M1.1 (PWM), U4.2 (SIG_A_OUT/IN)
unnamed: M2.1 (PWM), U4.3 (SIG_B_OUT/IN)
unnamed: M3.1 (PWM), U4.9 (SIG_C_OUT/IN)
unnamed: M4.1 (PWM), U4.10 (SIG_D_OUT/IN)
unnamed: M5.1 (PWM), U5.2 (SIG_A_OUT/IN)
unnamed: M6.1 (PWM), U5.3 (SIG_B_OUT/IN)
unnamed: M7.1 (+), U6.3 (1Y)
unnamed: M7.2 (-), U6.6 (2Y)
unnamed: U3.15 (QA), U4.13 (CONTROL_A)
unnamed: U3.1 (QB), U4.5 (CONTROL_B)
unnamed: U3.2 (QC), U4.6 (CONTROL_C)
unnamed: U3.3 (QD), U4.12 (CONTROL_D)
unnamed: U3.4 (QE), U5.13 (CONTROL_A)
unnamed: U3.5 (QF), U5.5 (CONTROL_B)
RCK: U1.6 (IO6), U3.12 (RCK)
SCK: U1.7 (IO7), U3.11 (SCK)
SCL: J2.1, U1.17 (IO9)
SDA: J2.2, U1.12 (IO8)
SERVO: U1.18 (IO10), U4.1 (SIG_A_IN/OUT), U4.4 (SIG_B_IN/OUT), U4.8 (SIG_C_IN/OUT), U4.11 (SIG_D_IN/OUT), U5.1 (SIG_A_IN/OUT), U5.4 (SIG_B_IN/OUT)
SI: U1.5 (IO5), U3.14 (SI)
ShiftH: J9.2, U3.7 (QH)
ShiftQ: J9.1, U3.6 (QG)
VCC_5V: C5.1, C6.1, J2.3, J5.1, J5.2, J5.3, J5.4, J8.2, M1.2 (+), M2.2 (+), M3.2 (+), M4.2 (+), M5.2 (+), M6.2 (+), U2.3 (VIN), U6.16 (VCC1)

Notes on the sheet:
Niet gebruiken: GPIO43-GPIO44,GPIO19-GPIO20 Strapping Pins: GPIO0,GPIO3,GPIO45,GPIO46
AUTOMATISCH INWERPEN
BUZZER
MOUNTING HOLES
USB-C
SERVO STURING
LCD
CONNECTORS
SPANNING REGELAAR
KNOPPEN
ESP32-S3-WROOM

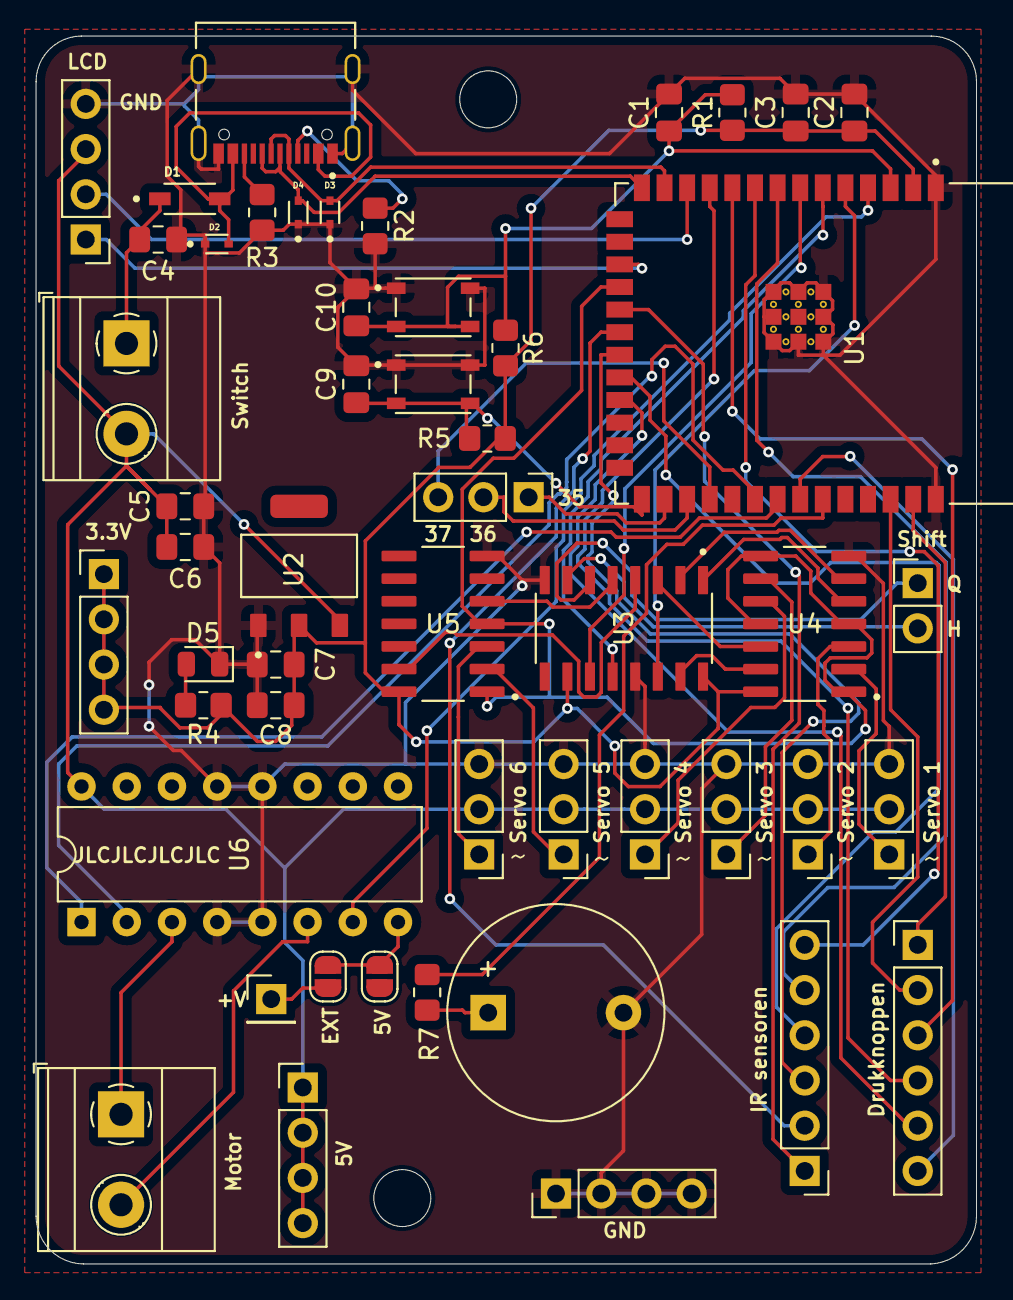
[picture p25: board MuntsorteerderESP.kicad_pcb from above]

Board: 2 copper layers, 52.8 x 69.0 mm, 53 parts (0 on the bottom side), 56 nets.

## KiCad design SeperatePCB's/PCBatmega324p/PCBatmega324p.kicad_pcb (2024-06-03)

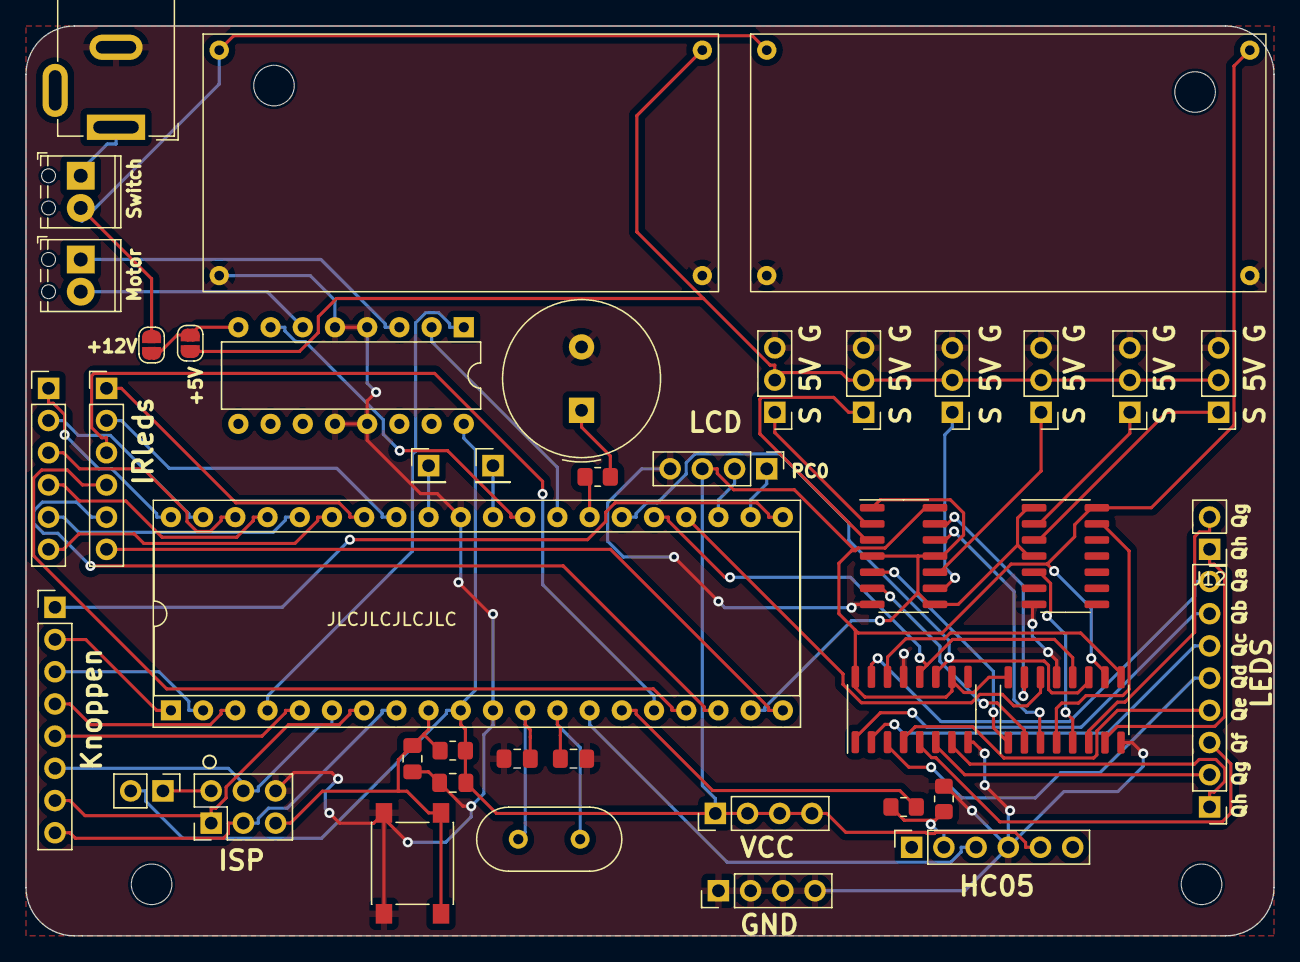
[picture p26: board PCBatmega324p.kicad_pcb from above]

Board: 2 copper layers, 98.4 x 71.8 mm, 47 parts (0 on the bottom side), 71 nets.

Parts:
BZ1: Buzzer; Buzzer_TDK_PS1240P02BT_D12.2mm_H6.5mm
C13, C18: 100nF; C_0805_2012Metric_Pad1.18x1.45mm_HandSolder
C16, C17: 22pF; C_0805_2012Metric_Pad1.18x1.45mm_HandSolder
H1, H2, H3, H4: MountingHole; MountingHole_3.2mm_M3
J1: Barrel_Jack; BarrelJack_GCT_DCJ200-10-A_Horizontal
J2: Conn_01x06_Socket; PinSocket_1x06_P2.54mm_Vertical
J3: AVR-ISP-6; PinHeader_2x03_P2.54mm_Vertical
J5: LCDconn; PinHeader_1x04_P2.54mm_Vertical
J6: Screw_Terminal_01x02; TerminalBlock_Phoenix_MPT-0,5-2-2.54_1x02_P2.54mm_Horizontal
J7, J8: portD_21; PinHeader_1x01_P2.54mm_Vertical
J9, J10: Conn_01x04_Pin; PinHeader_1x04_P2.54mm_Vertical
J11, J14: Conn_01x06_Pin; PinHeader_1x06_P2.54mm_Vertical
J12: Conn_01x02_Pin; PinHeader_1x02_P2.54mm_Vertical
J13, J15: Conn_01x08_Pin; PinHeader_1x08_P2.54mm_Vertical
JP1, JP2: SolderJumper_2_Open; SolderJumper-2_P1.3mm_Open_RoundedPad1.0x1.5mm
JP7: Jumper_2_Open; PinHeader_1x02_P2.54mm_Vertical
M1: Motor_DC; TerminalBlock_Phoenix_MPT-0,5-2-2.54_1x02_P2.54mm_Horizontal
M2, M3, M4, M5, M6, M7: Motor_Servo; PinHeader_1x03_P2.54mm_Vertical
R1, R2, R45: 10KΩ; R_0805_2012Metric_Pad1.20x1.40mm_HandSolder
R33: 100; R_0805_2012Metric_Pad1.20x1.40mm_HandSolder
SW9: SW_Push; SW_SPST_PTS645
U1: L293D; DIP-16_W7.62mm
U10, U11: Buck_Converter
U15: ATmega324P-20P; DIP-40_W15.24mm_Socket
U20, U21: 74HC595; SO-16_3.9x9.9mm_P1.27mm
U22, U23: CD4066BE; SO-14_3.9x8.65mm_P1.27mm
Y1: Crystal; Crystal_HC49-4H_Vertical

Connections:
+5V: JP2.2 (B), M2.2 (+), M3.2 (+), M4.2 (+), M5.2 (+), M6.2 (+), M7.2 (+), U10.OUT+
+12V: J6.2, JP1.2 (B), U10.IN+, U11.IN+
/AREF: J7.1, U15.32 (AREF)
/AVCC: J8.1, U15.30 (AVCC)
GND: BZ1.2 (+), C13.2, C16.2, C17.2, C18.1, J1.2, J2.4, J3.6 (GND), J5.4, J10.1, J10.2, J10.3, J10.4, M2.3 (-), M3.3 (-), M4.3 (-), M5.3 (-), M6.3 (-), M7.3 (-), R2.2, SW9.1, U1.4 (GND), U1.5 (GND), U1.12 (GND), U1.13 (GND), U10.IN-, U10.OUT-, U11.IN-, U11.OUT-, U15.11 (GND), U15.31 (GND), U20.8 (GND), U20.13 (~OE), U21.8 (GND), U21.13 (~OE), U22.7 (V_{SS}), U23.7 (V_{SS})
unnamed: BZ1.1 (-), R33.2
unnamed: J2.2, R1.2, R2.1
unnamed: J3.2 (VCC), JP7.1 (A)
unnamed: J1.1, J6.1
unnamed: J12.1, U20.7 (QH)
unnamed: J12.2, U20.6 (QG)
unnamed: J13.1, U21.7 (QH)
unnamed: J13.2, U21.6 (QG)
unnamed: J13.3, U21.5 (QF)
unnamed: J13.4, U21.4 (QE)
unnamed: J13.5, U21.3 (QD)
unnamed: J13.6, U21.2 (QC)
unnamed: J13.7, U21.1 (QB)
unnamed: J13.8, U21.15 (QA)
unnamed: JP1.1 (A), JP2.1 (A), U1.8 (VCC2)
unnamed: M1.1 (+), U1.3 (1Y)
unnamed: M1.2 (-), U1.6 (2Y)
unnamed: M2.1 (PWM), U23.2
unnamed: M3.1 (PWM), U23.3
unnamed: M4.1 (PWM), U23.9
unnamed: M5.1 (PWM), U23.10
unnamed: M6.1 (PWM), U22.2
unnamed: M7.1 (PWM), U22.3
unnamed: C16.1, U15.13 (XTAL1), Y1.2
unnamed: C17.1, U15.12 (XTAL2), Y1.1
unnamed: U20.15 (QA), U23.13
unnamed: U20.1 (QB), U23.5
unnamed: U20.2 (QC), U23.6
unnamed: U20.3 (QD), U23.12
unnamed: U20.4 (QE), U22.13
unnamed: U20.5 (QF), U22.5
unnamed: U20.9 (QH'), U21.14 (SER)
PA0: J11.1, U15.40 (PA0)
PA1: J11.2, U15.39 (PA1)
PA2: J11.3, U15.38 (PA2)
PA3: J11.4, U15.37 (PA3)
PA4: J11.5, U15.36 (PA4)
PA5: J11.6, U15.35 (PA5)
PA6: J14.1, U15.34 (PA6)
PA7: J14.2, U15.33 (PA7)
PB0: J15.2, U15.1 (PB0)
PB1: J15.3, U15.2 (PB1)
PB2: J15.4, U15.3 (PB2)
PB3: U1.1 (EN1,2), U15.4 (PB3)
PB4: J15.5, U15.5 (PB4)
PB5: J3.4 (MOSI), J15.6, U15.6 (PB5)
PB6: J3.1 (MISO), J15.7, U15.7 (PB6)
PB7: J3.3 (SCK), J15.8, U15.8 (PB7)
PC0: J5.1, U15.22 (PC0)
PC1: J5.2, U15.23 (PC1)
PC2: U15.24 (PC2), U20.14 (SER)
PC3: U15.25 (PC3), U20.12 (RCLK), U21.12 (RCLK)
PC4: U15.26 (PC4), U20.11 (SRCLK), U21.11 (SRCLK)
PC5: R33.1, U15.27 (PC5)
PC6: U1.2 (1A), U15.28 (PC6)
PC7: U1.7 (2A), U15.29 (PC7)
PD0: J2.3, U15.14 (PD0)
PD1: R1.1, U15.15 (PD1)
PD2: J14.3, U15.16 (PD2)
PD3: J14.4, U15.17 (PD3)
PD4: J14.5, U15.18 (PD4)
PD5: U15.19 (PD5), U22.1, U22.4, U23.1, U23.4, U23.8, U23.11
PD6: J14.6, U15.20 (PD6)
PD7: J15.1, U15.21 (PD7)
VCC: C18.2, J2.5, J5.3, J9.1, J9.2, J9.3, J9.4, JP7.2 (B), R45.1, U1.16 (VCC1), U11.OUT+, U15.10 (VCC), U20.10 (~SRCLR), U20.16 (VCC), U21.10 (~SRCLR), U21.16 (VCC), U22.14 (V_{DD}), U23.14 (V_{DD})
reset: C13.1, J3.5 (~RST), R45.2, SW9.2, U15.9 (~RESET)

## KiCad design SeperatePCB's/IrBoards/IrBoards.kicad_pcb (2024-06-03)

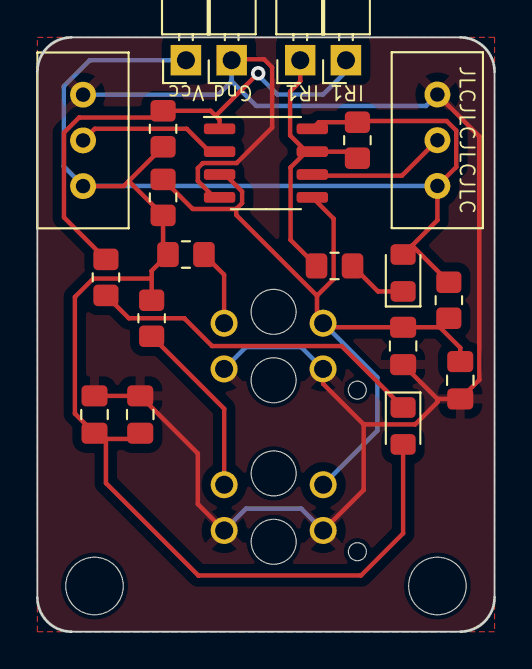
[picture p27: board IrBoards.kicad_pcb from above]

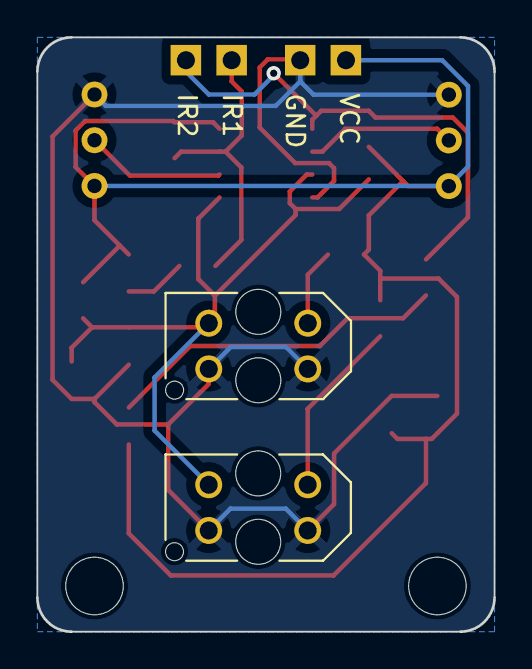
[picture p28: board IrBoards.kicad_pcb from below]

Board: 2 copper layers, 25.4 x 33.0 mm, 25 parts (2 on the bottom side), 11 nets.

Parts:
C1, C2, C3, C4: 0.1uF; C_0805_2012Metric_Pad1.18x1.45mm_HandSolder
D1, D2: LED; LED_0805_2012Metric_Pad1.15x1.40mm_HandSolder
H1, H2: MountingHole; MountingHole_3.2mm_M3
J2, J4, J5, J6: Conn_01x01_Pin; PinHeader_1x01_P2.54mm_Horizontal
R1, R5: 180; R_0805_2012Metric_Pad1.20x1.40mm_HandSolder
R2, R3, R6, R7: 10k; R_0805_2012Metric_Pad1.20x1.40mm_HandSolder
R4, R8: 1k; R_0805_2012Metric_Pad1.20x1.40mm_HandSolder
RV1, RV2: 10k; Potentiometer_Bourns_3296W_Vertical
U1: LM393; SO-8_3.9x4.9mm_P1.27mm
U2, U4: TCRT5000; OPTO_TCRT5000

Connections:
/irA0: C2.1, C4.1, R2.2, R6.2, U1.3 (+), U1.5 (+), U2.COLL, U4.COLL
GND: C1.2, C2.2, C3.2, C4.2, J4.1, RV1.3, RV2.3, U1.4 (V-), U2.CATH, U2.E, U4.CATH, U4.E
unnamed: D1.1 (K), R4.1
unnamed: D2.1 (K), R8.1
unnamed: J5.1, R3.2, R4.2, U1.1
unnamed: J6.1, R7.2, R8.2, U1.7
unnamed: R1.2, U2.A
unnamed: R5.2, U4.A
unnamed: RV1.2, U1.2 (-)
unnamed: RV2.2, U1.6 (-)
VCC: C1.1, C3.1, D1.2 (A), D2.2 (A), J2.1, R1.1, R2.1, R3.1, R5.1, R6.1, R7.1, RV1.1, RV2.1, U1.8 (V+)

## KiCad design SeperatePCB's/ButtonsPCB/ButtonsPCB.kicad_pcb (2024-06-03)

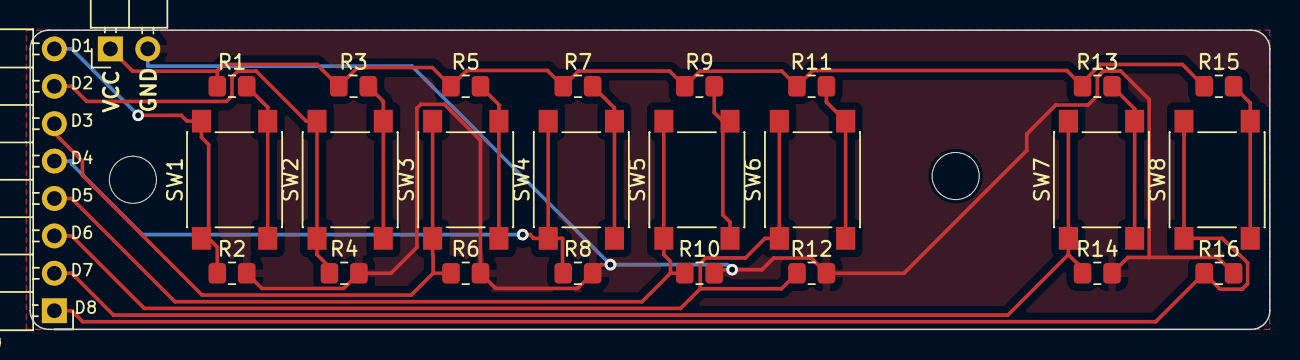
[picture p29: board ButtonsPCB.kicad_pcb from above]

Board: 2 copper layers, 84.2 x 20.3 mm, 28 parts (0 on the bottom side), 18 nets.

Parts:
H1, H2: MountingHole; MountingHole_3.2mm_M3
J1: Conn_01x02_Pin; PinHeader_1x02_P2.54mm_Horizontal
J9: Conn_01x08_Pin; PinHeader_1x08_P2.54mm_Horizontal
R1, R3, R5, R7, R9, R11, R13, R15: 470Ω; R_0805_2012Metric_Pad1.20x1.40mm_HandSolder
R2, R4, R6, R8, R10, R12, R14, R16: 10KΩ; R_0805_2012Metric_Pad1.20x1.40mm_HandSolder
SW1, SW2, SW3, SW4, SW5, SW6, SW7, SW8: SW_Push; SW_SPST_PTS645

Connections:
GND: J1.2, R2.2, R4.2, R6.2, R8.2, R10.2, R12.2, R14.2, R16.2
unnamed: J9.1, R16.1, SW8.1
unnamed: J9.2, R14.1, SW7.1
unnamed: J9.3, R12.1, SW6.1
unnamed: J9.4, R10.1, SW5.1
unnamed: J9.5, R8.1, SW4.1
unnamed: J9.6, R6.1, SW3.1
unnamed: J9.7, R4.1, SW2.1
unnamed: J9.8, R2.1, SW1.1
unnamed: R1.2, SW1.2
unnamed: R3.2, SW2.2
unnamed: R5.2, SW3.2
unnamed: R7.2, SW4.2
unnamed: R9.2, SW5.2
unnamed: R11.2, SW6.2
unnamed: R13.2, SW7.2
unnamed: R15.2, SW8.2
VCC: J1.1, R1.1, R3.1, R5.1, R7.1, R9.1, R11.1, R13.1, R15.1

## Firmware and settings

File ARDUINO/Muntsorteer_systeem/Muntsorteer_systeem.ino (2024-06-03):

#include <LiquidCrystal_I2C.h> //LCD bibliotheek gebruiken
#include <ESP32Servo.h> //Servo bibliotheek gebruiken
#include "BluetoothSerial.h" //Bluetooth bibliotheek gebruiken
#include "pitches.h"
#include <EEPROM.h>

#define BUZZZER_PIN  27 // ESP32 pin GPIO18 connected to piezo buzzer

#define knop5cent_PIN  15 // Knop om 5 cent uit te werpen
#define knop10cent_PIN  2 // Knop om 10 cent uit te werpen
#define knop20cent_PIN  0 // Knop om 20 cent uit te werpen
#define knop50cent_PIN  23 // Knop om 50 cent uit te werpen
#define knop1euro_PIN  32 // Knop om 1 euro uit te werpen
#define knop2euro_PIN  35 // Knop om 2 euro uit te werpen

int melody[] = {
  NOTE_C4, NOTE_G3, NOTE_G3, NOTE_A3, NOTE_G3, 0, NOTE_B3, NOTE_C4
};

int noteDurations[] = {
  4, 8, 8, 4, 4, 4, 4, 4
};

LiquidCrystal_I2C lcd(0x27,16,2);  //lcd object maken met LCD I2c adres 0x27

byte euro[8] = {
	0b00111,
	0b01000,
	0b11100,
	0b01000,
	0b01000,
	0b11100,
	0b01000,
	0b00111
};

String device_name = "Muntsorteer- en opslagsysteem"; //Bluetooth naam instellen

String message = ""; //Inkomende string
char incomingChar; //Inkomende char

//Ter controle voor als bluetooth niet enabled is in de esp
#if !defined(CONFIG_BT_ENABLED) || !defined(CONFIG_BLUEDROID_ENABLED)
#error Bluetooth is not enabled! Please run `make menuconfig` to and enable it
#endif

#if !defined(CONFIG_BT_SPP_ENABLED)
#error Serial Bluetooth not available or not enabled. It is only available for the ESP32 chip.
#endif

BluetoothSerial SerialBT; //Object maken voor seriële bluetooth

//SDA 21, SCL 22

//Een structuur maken voor elk geldtype
struct munt {
	const uint8_t PIN;
	uint32_t aantal;
  uint32_t maxAantal;
};

munt cent5 = {33, 0, 3}; //Instantie maken voor 5 cent
munt cent10 = {16, 0, 3}; //Instantie maken voor 10 cent
munt cent20 = {17, 0, 3}; //Instantie maken voor 20 cent
munt cent50 = {5, 0, 3}; //Instantie maken voor 50 cent
munt eur1 = {18, 0, 3}; //Instantie maken voor 1 euro
munt eur2 = {19, 0, 3}; //Instantie maken voor 2 euro

bool bedragVerandert = false;
//Variabelen die zorgen voor de timing van de interrupts
unsigned long button_time = 0;  
unsigned long last_button_time = 0; 

//Pin verbonden met ST_CP van de 74HC595
int latchPin = 4;
//Pin verbonden met SH_CP van de 74HC595
int clkPin = 12;
//Pin verbonden met DS van de 74HC595
int dtPin = 14;
//Pin die verbonden is met het servo signaal
int servoPin = 13;

bool btn5c = false;
bool btn10c = false;
bool btn20c = false;
bool btn50c = false;
bool btn1eur = false;
bool btn2eur = false;

bool cent5Vol;
bool cent10Vol;
bool cent20Vol;
bool cent50Vol;
bool eur1Vol;
bool eur2Vol;



Servo myservo;  // Servo object maken om de servo te besturen

String stringOmTeVerzenden = ""; //String die gebruikt zal worden voor het verzenden

//Interrupt voor 10 cent
void IRAM_ATTR isr10c() {
  button_time = millis();
  if (button_time - last_button_time > 250)
    {
      if(cent10.aantal >= cent10.maxAantal){
        cent10Vol = true;
      }
      cent10.aantal++;
      String verzendString = "O10c" + String(cent10.aantal) + "\n";
      SerialBT.print(verzendString);
      bedragVerandert = true;
      last_button_time = button_time;
    }
}

//Interrupt voor 5 cent
void IRAM_ATTR isr5c() {
  button_time = millis();
  if (button_time - last_button_time > 250)
    {
      if(cent5.aantal >= cent5.maxAantal){
        cent5Vol = true;
      }
      cent5.aantal++;
      String verzendString = "O5c" + String(cent5.aantal) + "\n";
      SerialBT.print(verzendString);
      bedragVerandert = true;
      last_button_time = button_time;
    }
}

//Interrupt voor 20 cent
void IRAM_ATTR isr20c() {
  button_time = millis();
  if (button_time - last_button_time > 250)
    {
      if(cent20.aantal >= cent20.maxAantal){
        cent20Vol = true;
      }
      cent20.aantal++;
      String verzendString = "O20c" + String(cent20.aantal) + "\n";
      SerialBT.print(verzendString);
      bedragVerandert = true;
      last_button_time = button_time;
    }
}

//Interrupt voor 50 cent
void IRAM_ATTR isr50c() {
  button_time = millis();
  if (button_time - last_button_time > 250)
    {
      if(cent50.aantal >= cent50.maxAantal){
        cent50Vol = true;
      }
      cent50.aantal++;
      String verzendString = "O50c" + String(cent50.aantal) + "\n";
      SerialBT.print(verzendString);
      bedragVerandert = true;
      last_button_time = button_time;
    }
}

//Interrupt voor 1 euro
void IRAM_ATTR isr1eur() {
  button_time = millis();
  if (button_time - last_button_time > 250)
    {
      if(eur1.aantal >= eur1.maxAantal){
        eur1Vol = true;
      }
      eur1.aantal++;
      String verzendString = "O100c" + String(eur1.aantal) + "\n";
      SerialBT.print(verzendString);
      bedragVerandert = true;
      last_button_time = button_time;
    }
}

//Interrupt voor 2 euro
void IRAM_ATTR isr2eur() {
  button_time = millis();
  if (button_time - last_button_time > 250)
    {
      if(eur2.aantal >= eur2.maxAantal){
        eur2Vol = true;
      }
      eur2.aantal++;
      String verzendString = "O200c" + String(eur2.aantal) + "\n";
      SerialBT.print(verzendString);
      bedragVerandert = true;
      last_button_time = button_time;
    }
}

void setup() {
  lcd.init();
  lcd.createChar(0, euro);
  lcd.clear();         
  lcd.backlight();   
  updateLCD("GIPTiebeDeclercq", "test");  

  SerialBT.begin(device_name); //Bluetooth naam instellen
  Serial.begin(115200); //Communicatie beginnen voor in de serial monitor te debuggen

	pinMode(cent10.PIN, INPUT);
  pinMode(cent5.PIN, INPUT);
	pinMode(cent20.PIN, INPUT);
  pinMode(cent50.PIN, INPUT);
  pinMode(eur1.PIN, INPUT);
  pinMode(eur2.PIN, INPUT);

  pinMode(knop5cent_PIN, INPUT);
  pinMode(knop10cent_PIN, INPUT);
  pinMode(knop20cent_PIN, INPUT);
  pinMode(knop50cent_PIN, INPUT);
  pinMode(knop1euro_PIN, INPUT);
  pinMode(knop2euro_PIN, INPUT);
  
	attachInterrupt(cent10.PIN, isr10c, FALLING);
  attachInterrupt(cent5.PIN, isr5c, FALLING);
  attachInterrupt(cent20.PIN, isr20c, FALLING);
  attachInterrupt(cent50.PIN, isr50c, FALLING);
  attachInterrupt(eur1.PIN, isr1eur, FALLING);
  attachInterrupt(eur2.PIN, isr2eur, FALLING);

  // de 74HC595 pinnen als uitgangen instellen
  pinMode(latchPin, OUTPUT);    //ST_CP pin van de 74HC595
  pinMode(clkPin, OUTPUT);      //SH_CP pin van de 74HC595
  pinMode(dtPin, OUTPUT);       //DS pin van de 74HC595

  for (int thisNote = 0; thisNote < 8; thisNote++) {
    int noteDuration = 1000 / noteDurations[thisNote];
    tone(BUZZZER_PIN, melody[thisNote], noteDuration);

    int pauseBetweenNotes = noteDuration * 1.30;
    delay(pauseBetweenNotes);
    noTone(BUZZZER_PIN);
  }

  // Alle timer allocaten voor de servo
	ESP32PWM::allocateTimer(0);
	ESP32PWM::allocateTimer(1);
	ESP32PWM::allocateTimer(2);
	ESP32PWM::allocateTimer(3); 
	myservo.setPeriodHertz(50);    // standaard 50 hz servo
	myservo.attach(servoPin, 500, 2400); // Servo verbinden met de servopin

}

void loop() {
  if (SerialBT.available()) { //Enkel als je bluetooth hebt uitvoeren
    char incomingChar = SerialBT.read(); //Inkomende data lezen
    if (incomingChar != '\n'){ //Nog niet het einde van de verzonden data
      message += String(incomingChar); //Char toevoegen aan de string
    }
    else{ //Einde verzonden data
      dataVerwerken(message); //Deze data verwerken
      message = "";
    }
    Serial.write(incomingChar); //In de serial monitor de data sturen voor debuggen 
  }
  delay(20);
  if(bedragVerandert){
    updateLCD("Totale bedrag:", String(totaleBedrag())+" euro");
    bedragVerandert = false;
  }

  if(digitalRead(knop5cent_PIN) && !btn5c){
    dispenseCoin(5);
    btn5c = true;
  }
  else if(!digitalRead(knop5cent_PIN) && btn5c){
    btn5c = false;
  }
  if (digitalRead(knop10cent_PIN) && !btn10c){
    dispenseCoin(10);
    btn10c = true;
  }else if(!digitalRead(knop10cent_PIN) && btn10c){
    btn10c = false;
  }
  /*if (digitalRead(knop20cent_PIN)){
    Serial.write("knop20c");
    dispenseCoin(20);
  }*/
  if (digitalRead(knop50cent_PIN) && !btn50c){
    dispenseCoin(50);
    btn50c= true;
  }else if(!digitalRead(knop50cent_PIN) && btn50c){
    btn50c= false;
  }
  if (digitalRead(knop1euro_PIN) && !btn1eur){
    dispenseCoin(100);
    btn1eur = true;
  }else if(!digitalRead(knop1euro_PIN) && btn1eur){
    btn1eur = false;
  }
  if (digitalRead(knop2euro_PIN) && !btn2eur){
    dispenseCoin(200);
    btn2eur = true;
  }else if(!digitalRead(knop2euro_PIN) && btn2eur){
    btn2eur = false;
  }

  if(cent5Vol){
    dispenseCoin(5);
    cent5Vol = false;
  }
  if(cent10Vol){
    dispenseCoin(10);
    cent10Vol = false;
  }
  if(cent20Vol){
    dispenseCoin(20);
    cent20Vol = false;
  }
  if(cent50Vol){
    dispenseCoin(50);
    cent50Vol = false;
  }
  if(eur1Vol){
    dispenseCoin(100);
    eur1Vol = false;
  }
  if(eur2Vol){
    dispenseCoin(200);
    eur2Vol = false;
  }
}

float totaleBedrag(){
  return (eur2.aantal * 2 + eur1.aantal + cent50.aantal * 0.5 + cent20.aantal * 0.2 + cent10.aantal * 0.1 + cent5.aantal * 0.05);
}

void updateLCD(String firstline, String secondLine){
  lcd.clear();
  lcd.setCursor(0, 0);
  lcd.print(firstline);
  lcd.setCursor(0, 1);
  lcd.write(0);
  lcd.setCursor(1, 1);
  lcd.print(secondLine);
}

//Data verwerken
void dataVerwerken(String verzondenData){
  char firstLetter = verzondenData.charAt(0); //Eerste karakter inlezen
  if(firstLetter == 's'){ //Geldtype uitwerpen
    String derestVanDeString = verzondenData.substring(1);
    if (derestVanDeString == "5"){
      dispenseCoin(5);
    }
    else if (derestVanDeString == "10"){
      dispenseCoin(10);
    }
    else if (derestVanDeString == "20"){
    dispenseCoin(20);
    }
    else if (derestVanDeString == "50"){
    dispenseCoin(50);
    }
    else if (derestVanDeString == "1"){
    dispenseCoin(100);
    }
      else if (derestVanDeString == "2"){
    dispenseCoin(200);
    }
  }
  else if(firstLetter == 'l'){ //LCD aan/af
    char secondLetter = verzondenData.charAt(1);
    if(secondLetter == 's'){
      String tekst = verzondenData.substring(2);
      lcd.clear();
      lcd.setCursor(0, 0);
      lcd.print(tekst);
      Serial.println(tekst);
    }
    else{
      String derestVanDeString = verzondenData.substring(1);
      if(derestVanDeString == "1"){ //LCD aan
        lcd.backlight();
      }
      else{ //LCD af
        lcd.noBacklight();
      }
    }
  }
  else if (message == "v"){ //Programma is net verbonden
    //Alle huidige geldwaarden doorsturen
    SerialBT.print("O200c" + String(eur2.aantal) + "\n");
    delay(50);
    SerialBT.print("O100c" + String(eur1.aantal) + "\n");
    delay(50);
    SerialBT.print("O50c" + String(cent50.aantal) + "\n");
    delay(50);
    SerialBT.print("O20c" + String(cent20.aantal) + "\n");
    delay(50);
    SerialBT.print("O10c" + String(cent10.aantal) + "\n");
    delay(50);
    SerialBT.print("O5c" + String(cent5.aantal) + "\n");
  }
}
//Een geldtype uitwerpen
void dispenseCoin(int amount){
  switch(amount){
    case 5: //5 cent
      if(cent5.aantal > 0){ //Enkel uitvoeren als je geld van deze soort hebt
        updateShiftRegister(0b01000000);
        cent5.aantal--;
        stringOmTeVerzenden = "O5c" + String(cent5.aantal) + "\n";
        SerialBT.print(stringOmTeVerzenden); //Versturen via bluetooth
        Serial.println(stringOmTeVerzenden);  //Serieel in de monitor versturen voor debug redenen
        //Daarna de servo aansturen
        myservo.write(180);
        delay(400); //Zorgen dat er genoeg tijd is voor de servo om te draaien
        myservo.write(0);
        bedragVerandert = true;
      }
      break;
    case 10: //10 cent
      if(cent10.aantal > 0){
      updateShiftRegister(0b10000000);
      cent10.aantal--;
      stringOmTeVerzenden = "O10c" + String(cent10.aantal) + "\n";
        SerialBT.print(stringOmTeVerzenden); //Versturen via bluetooth
        Serial.println(stringOmTeVerzenden);  //Serieel in de monitor versturen voor debug redenen
        //Daarna de servo aansturen
        myservo.write(180);
        delay(400); //Zorgen dat er genoeg tijd is voor de servo om te draaien
        myservo.write(0);
        bedragVerandert = true;
      }
      break;
    case 20: //20 cent
    if(cent20.aantal > 0){
      updateShiftRegister(0b00100000);
      cent20.aantal--;
      stringOmTeVerzenden = "O20c" + String(cent20.aantal) + "\n";
              SerialBT.print(stringOmTeVerzenden); //Versturen via bluetooth
        Serial.println(stringOmTeVerzenden);  //Serieel in de monitor versturen voor debug redenen
        //Daarna de servo aansturen
        myservo.write(180);
        delay(400); //Zorgen dat er genoeg tijd is voor de servo om te draaien
        myservo.write(0);
        bedragVerandert = true;
      }
      break;
    case 50: //50 cent
    if(cent50.aantal > 0){
      updateShiftRegister(0b00001000);
      cent50.aantal--;
      stringOmTeVerzenden = "O50c" + String(cent50.aantal) + "\n";
              SerialBT.print(stringOmTeVerzenden); //Versturen via bluetooth
        Serial.println(stringOmTeVerzenden);  //Serieel in de monitor versturen voor debug redenen
        //Daarna de servo aansturen
        myservo.write(180);
        delay(400); //Zorgen dat er genoeg tijd is voor de servo om te draaien
        myservo.write(0);
        bedragVerandert = true;
      }
      break;
    case 100: // 1 euro
    if(eur1.aantal > 0){
      updateShiftRegister(0b00010000);
      eur1.aantal--;
      stringOmTeVerzenden = "O100c" + String(eur1.aantal) + "\n";
              SerialBT.print(stringOmTeVerzenden); //Versturen via bluetooth
        Serial.println(stringOmTeVerzenden);  //Serieel in de monitor versturen voor debug redenen
        //Daarna de servo aansturen
        myservo.write(180);
        delay(400); //Zorgen dat er genoeg tijd is voor de servo om te draaien
        myservo.write(0);
        bedragVerandert = true;
      }
      break;
    case 200: // 2 euro
    if(eur2.aantal > 0){
      updateShiftRegister(0b00000100);
      eur2.aantal--;
      stringOmTeVerzenden = "O200c" + String(eur2.aantal) + "\n";
              SerialBT.print(stringOmTeVerzenden); //Versturen via bluetooth
        Serial.println(stringOmTeVerzenden);  //Serieel in de monitor versturen voor debug redenen
        //Daarna de servo aansturen
        myservo.write(180);
        delay(400); //Zorgen dat er genoeg tijd is voor de servo om te draaien
        myservo.write(0);
        bedragVerandert = true;
      }
      break;
  }
}

//Deze functie is voor het aansturen van het schuifregister
void updateShiftRegister(int uitgangen)
{
  digitalWrite(latchPin, LOW);
  shiftOut(dtPin, clkPin, LSBFIRST, uitgangen);
  digitalWrite(latchPin, HIGH);
}

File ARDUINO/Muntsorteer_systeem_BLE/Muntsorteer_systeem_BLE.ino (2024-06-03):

//Muntsorteer- en opslagsysteem
//(C)Tiebe Declercq 2024

#include <BLEDevice.h>
#include <BLEServer.h>
#include <BLEUtils.h>
#include <BLE2902.h>
#include <LiquidCrystal_I2C.h> //LCD bibliotheek gebruiken
#include <ESP32Servo.h> //Servo bibliotheek gebruiken
#include <EEPROM.h> 
#include "pitches.h"

BLEServer *pServer = NULL;
BLECharacteristic * pTxCharacteristic;
bool deviceConnected = false;
bool oldDeviceConnected = false;
uint8_t txValue = 0;

#define SERVICE_UUID           "6E400001-B5A3-F393-E0A9-E50E24DCCA9E" // UART service UUID
#define CHARACTERISTIC_UUID_RX "6E400002-B5A3-F393-E0A9-E50E24DCCA9E" //RX characteristic UUID
#define CHARACTERISTIC_UUID_TX "6E400003-B5A3-F393-E0A9-E50E24DCCA9E" //TX characteristic UUID

#define BUZZZER_PIN  27 // ESP32 pin GPIO18 connected to piezo buzzer

#define knop5cent_PIN  15 // Knop om 5 cent uit te werpen
#define knop10cent_PIN  2 // Knop om 10 cent uit te werpen
#define knop20cent_PIN  0 // Knop om 20 cent uit te werpen
#define knop50cent_PIN  23 // Knop om 50 cent uit te werpen
#define knop1euro_PIN  32 // Knop om 1 euro uit te werpen
#define knop2euro_PIN  35 // Knop om 2 euro uit te werpen

LiquidCrystal_I2C lcd(0x27,16,2);  //lcd object maken met LCD I2c adres 0x27

byte euro[8] = { //Speciaal euro teken voor LCD display
	0b00111,
	0b01000,
	0b11100,
	0b01000,
	0b01000,
	0b11100,
	0b01000,
	0b00111
};

//SDA 21, SCL 22

//Een structuur maken voor elk geldtype
struct munt {
	const uint8_t PIN;
	uint32_t aantal;
  uint32_t maxAantal;
};

munt cent5 = {33, 0, 20}; //Instantie maken voor 5 cent
munt cent10 = {16, 0, 20}; //Instantie maken voor 10 cent
munt cent20 = {17, 0, 20}; //Instantie maken voor 20 cent
munt cent50 = {5, 0, 20}; //Instantie maken voor 50 cent
munt eur1 = {18, 0, 20}; //Instantie maken voor 1 euro
munt eur2 = {19, 0, 20}; //Instantie maken voor 2 euro

bool bedragVerandert = false; //Bijhouden wanneer de lcd moet updaten naar ene nieuw bedrag

bool cent5changed = false; //Het 5 cent aantal is verandert 
bool cent10changed = false; //Het 10 cent aantal is verandert 
bool cent20changed = false; //Het 20 cent aantal is verandert 
bool cent50changed = false; //Het 50 cent aantal is verandert 
bool eur1changed = false; //Het 1 euro aantal is verandert 
bool eur2changed = false; //Het 2 euro aantal is verandert 

//Variabelen die zorgen voor de timing van de interrupts
unsigned long button_time = 0;  
unsigned long last_button_time = 0; 

//Pin verbonden met ST_CP van de 74HC595
int latchPin = 4;
//Pin verbonden met SH_CP van de 74HC595
int clkPin = 12;
//Pin verbonden met DS van de 74HC595
int dtPin = 14;
//Pin die verbonden is met het servo signaal
int servoPin = 13;

bool btn5c = false; 
bool btn10c = false;
bool btn20c = false;
bool btn50c = false;
bool btn1eur = false;
bool btn2eur = false;

bool customLcdModus = false; //LCD niet met de geldwaarde updaten
bool nietInlatenModus = false; //Niets meer in het systeem laten

Servo myservo;  // Servo object maken om de servo te besturen

String stringOmTeVerzenden = ""; //String die gebruikt zal worden voor het verzenden

bool boot = true; //1x bij opstart

int melody[] = {
  NOTE_C4, NOTE_G3, NOTE_G3, NOTE_A3, NOTE_G3, 0, NOTE_B3, NOTE_C4
};

int noteDurations[] = {
  4, 8, 8, 4, 4, 4, 4, 4
};

void dataVerwerken(String);

//Interrupt voor 10 cent
void IRAM_ATTR isr10c() {
  button_time = millis(); //Gebruik maken van millis zodat het niet onderbroken wordt
  if (button_time - last_button_time > 100) //Dender op de interrupt vermijden
    {
      cent10.aantal++;
      cent10changed = true;
      bedragVerandert = true;
      last_button_time = button_time;
    }
}

//Interrupt voor 5 cent
void IRAM_ATTR isr5c() {
  button_time = millis();
  if (button_time - last_button_time > 100)
    {
      cent5.aantal++;
      cent5changed = true;
      bedragVerandert = true;
      last_button_time = button_time;
    }
}

//Interrupt voor 20 cent
void IRAM_ATTR isr20c() {
  button_time = millis();
  if (button_time - last_button_time > 100)
    {
      cent20.aantal++;
      cent20changed = true;
      bedragVerandert = true;
      last_button_time = button_time;
    }
}

//Interrupt voor 50 cent
void IRAM_ATTR isr50c() {
  button_time = millis();
  if (button_time - last_button_time > 100)
    {
      cent50.aantal++;
      cent50changed = true;
      bedragVerandert = true;
      last_button_time = button_time;
    }
}

//Interrupt voor 1 euro
void IRAM_ATTR isr1eur() {
  button_time = millis();
  if (button_time - last_button_time > 50)
    {
      eur1.aantal++;
      eur1changed = true;
      bedragVerandert = true;
      last_button_time = button_time;
    }
}

//Interrupt voor 2 euro
void IRAM_ATTR isr2eur() {
  button_time = millis();
  if (button_time - last_button_time > 50)
    {
      eur2.aantal++;
      eur2changed = true;
      bedragVerandert = true;
      last_button_time = button_time;
    }
}

class MyServerCallbacks: public BLEServerCallbacks {
    void onConnect(BLEServer* pServer) {
      deviceConnected = true;
    };

    void onDisconnect(BLEServer* pServer) {
      deviceConnected = false;
    }
};

class MyCallbacks: public BLECharacteristicCallbacks {
    void onWrite(BLECharacteristic *pCharacteristic) {
    std::string rxValue = pCharacteristic->getValue();
    const char* cString = rxValue.c_str(); // Convert std::string to const char*
    String arduinoString = String(cString); // Convert const char* to Arduino String
    dataVerwerken(arduinoString);
    }
};


void setup() {
  lcd_INIT();
  Serial.begin(115200); //Serial monitor kunnen zien
  pinMode(BUZZZER_PIN, OUTPUT); //Buzzer ingang    
  irsensor_INIT();
  button_INIT();
	interrupt_INIT();
  schuifregister_INIT();
  servo_INIT();
  ble_INIT();
}

//Initialisatie voor je lcd
void lcd_INIT(){
  lcd.init();
  lcd.createChar(0, euro); //Custom char voor euro teken maken
  lcd.clear();         
  lcd.backlight();   
  updateLCD("GIPTiebeDeclercq", "0.0");  
}

//Initialisatie voor al je infrarood sensoren
void irsensor_INIT(){
  pinMode(cent10.PIN, INPUT);
  pinMode(cent5.PIN, INPUT);
	pinMode(cent20.PIN, INPUT);
  pinMode(cent50.PIN, INPUT);
  pinMode(eur1.PIN, INPUT);
  pinMode(eur2.PIN, INPUT);
}

//Initialisatie voor al je drukknoppen
void button_INIT(){
  pinMode(knop5cent_PIN, INPUT);
  pinMode(knop10cent_PIN, INPUT);
  pinMode(knop20cent_PIN, INPUT);
  pinMode(knop50cent_PIN, INPUT);
  pinMode(knop1euro_PIN, INPUT);
  pinMode(knop2euro_PIN, INPUT);
}

//Initialisatie voor je interrupt
void interrupt_INIT(){
	attachInterrupt(cent10.PIN, isr10c, FALLING);
  attachInterrupt(cent5.PIN, isr5c, FALLING);
  attachInterrupt(cent20.PIN, isr20c, FALLING);
  attachInterrupt(cent50.PIN, isr50c, FALLING);
  attachInterrupt(eur1.PIN, isr1eur, FALLING);
  attachInterrupt(eur2.PIN, isr2eur, FALLING);
}
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
